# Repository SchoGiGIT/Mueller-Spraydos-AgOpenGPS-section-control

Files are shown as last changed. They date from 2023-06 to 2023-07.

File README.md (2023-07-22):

# Mueler Spraydos AgOpenGPS section control
An electromechanical approach to open source section control of Mueler/Müller Spraydos spraying computers through software as AgOpenGPS. 
This project provides the mechanical design for a non-intrusive addon mod to automatically control the sections on a spraydos computer through a gps system. All needed parts and other information are discribed bellow.

The system consists out of a bracket, that clamps around the spraying computer and doubles as electronics box, and a servo box on a hinge. The main section switch and all other buttons remain freely accessible.

<p float="left">
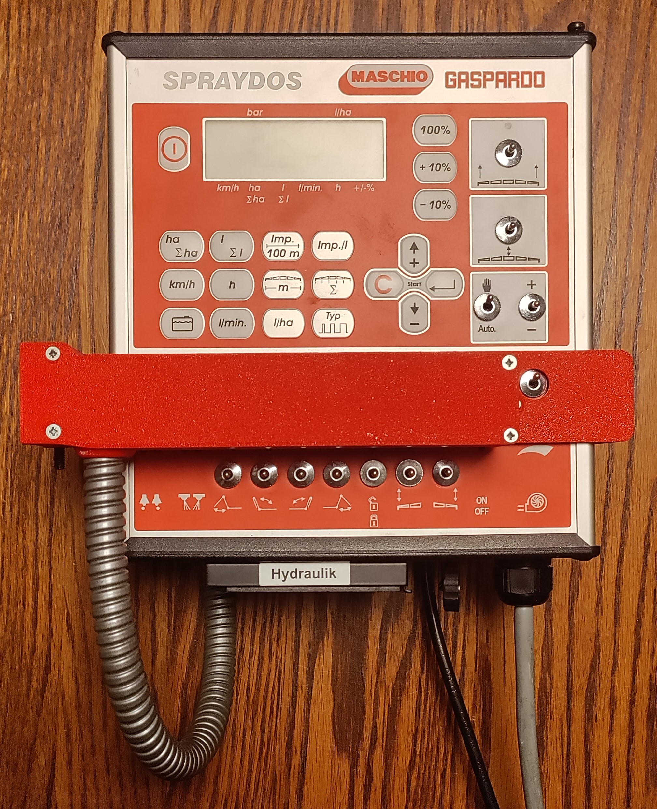
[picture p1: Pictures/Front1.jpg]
  
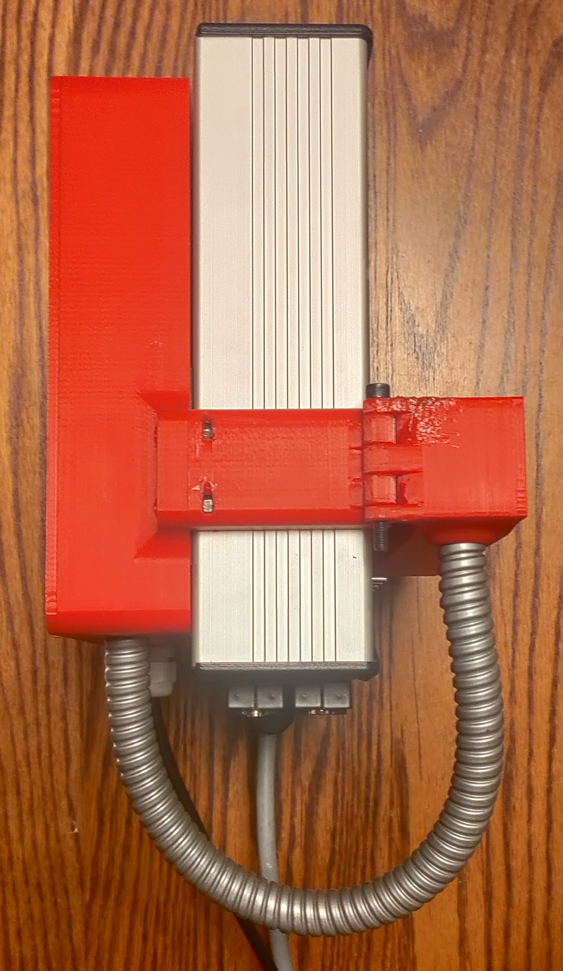
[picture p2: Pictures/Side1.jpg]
  
</p>

The servo box contains servos to control the section switches through specially designed lever arms. The servo box is mounted on a hinge and can be swung away to regain manual control. The servo box can be kept closed through magnets or an M4 bolt
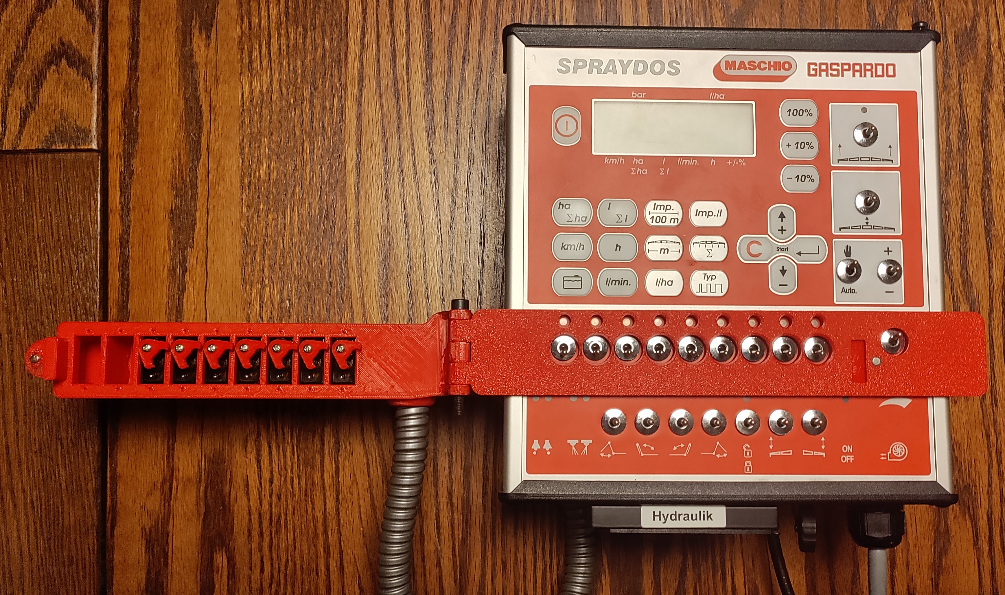
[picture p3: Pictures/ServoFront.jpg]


The electronics box on the back has mounting points to accommodate a 8ch servo controller, A DC buck converter and a 8 channel relay card (optional). The optional relay card can be replaced with a second servo controller when you need 9 sections (mounting holes are there in the new models). Two 16mm holes for input power and section signals and a threaded hole for a sleeve to the Servo box are foreseen.
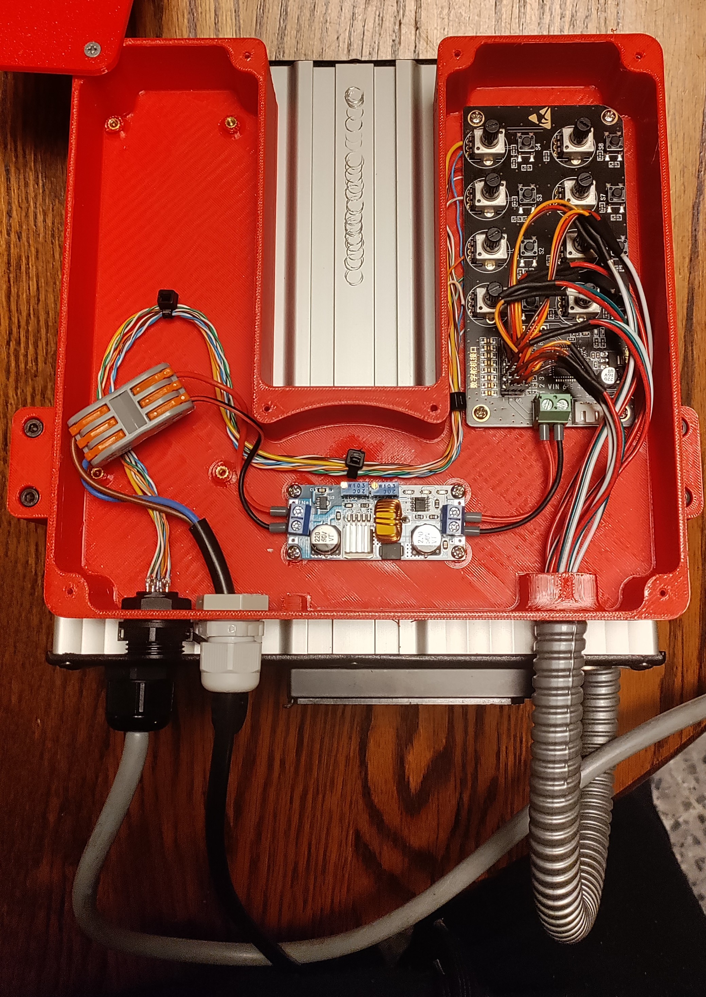
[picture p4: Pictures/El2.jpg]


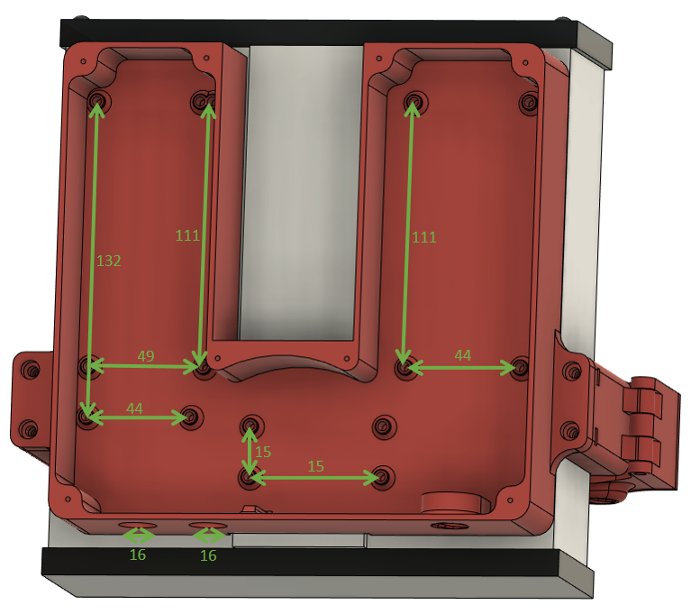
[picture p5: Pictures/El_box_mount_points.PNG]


**_Why control the buttons mechanically and not switch section through relays?_**
* Motorised valves need 2 relays per section (18 in total...).
* You cannot put relays in parallel to the buttons, you will create a short.
* To keep the switches as manual backup they cannot be replaced by relays.
* Breaking the lines going to the the valves and changing the state there with relays could work. But the rate controller will not work anymore since it does not know the real state of the sections. (You could compensate this by changeing the speed signal however)
* To keep the mod as a bolt-on add on to keep the controller original for resale when the time comes.

## Needed hardware
### Printed parts
I provide some limited print service for Western europe. Contact me through github or on [this thread](https://discourse.agopengps.com/t/printing-service-for-aog-community-western-europe/12823)

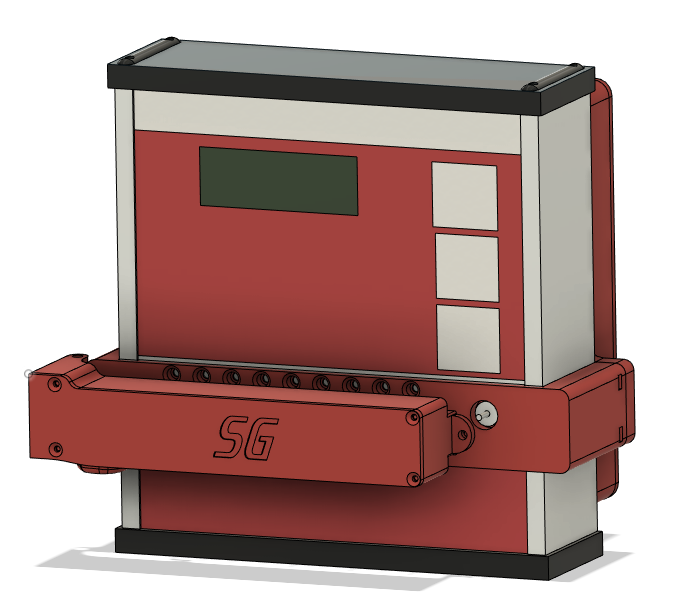
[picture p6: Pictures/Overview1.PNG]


* [Servo box](/Printed_parts/ServoBox.step)
* [Servo box lid](/Printed_parts/ServoBoxLid.step)
* Front bracket
  * [Normal nut](/Printed_parts/FrontBracket.step)
  * [Hotmelt nut](/Printed_parts/FrontBracketHot.step)
* [Electronics box](/Printed_parts/ElBox.step)
* [Electronics box lid](/Printed_parts/ElBoxLid.step)
* [Servo arm](/Printed_parts/ServoArm.step)

### Montage parts
* Wood screw D3 l15 X14 (for al the lids)
* Bolt M4 l15 X4 (for mounting the bracket to the electronics box)
* For mounting the bracket to the electronics box (one of the two)
  * Nut M4 X4
  * Hotmelt nut M4 X4
* Bolt M5 l45 X1 (Serves as hinge bolt)
* Nut M5 X1 (Serves as hinge bolt)
* Hot melt nut M3 X12
* Closing latch (one of the two)
  * Magnet D5 L5 X2 (push in with solder iron)
  * Bolt M4 l8 + Nut M4
* EPDM roofing sheet (+-1mm thick)
  * Glue a big patch or multiple smaller ones on the back of the electronics box. This will provide extra mounting friction and adapt better to the uneven surface of the spraydos controller  

### Electronics
For more than 8 sections you will need two servo controllers or a different type that can accommodate 9 servos.
* Servo motor MG90S (as many as needed for your sprayer) (other models might fit, did not try)
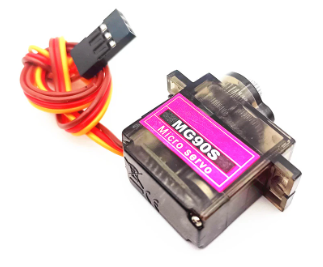
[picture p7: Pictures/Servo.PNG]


* Servo controller, i used [this one](https://nl.aliexpress.com/item/1005002120074314.html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) :
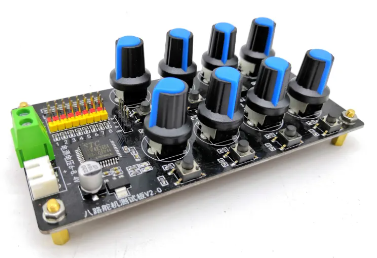
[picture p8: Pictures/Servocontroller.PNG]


* DC buck converter XL4015 5A, mounting holes are compatible with [CC/CV models like this one](https://nl.aliexpress.com/item/1005002554895443.html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) :
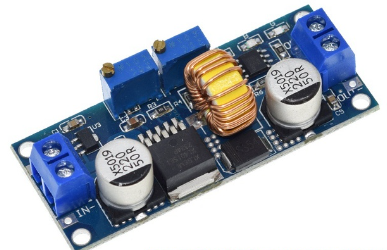
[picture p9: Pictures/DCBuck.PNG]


* Optional 8 way relay module, mounting holes are compatible with [this one](https://nl.aliexpress.com/item/1005002867727977.html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) :
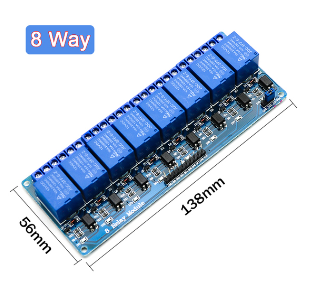
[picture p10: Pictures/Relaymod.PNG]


* Wire nuts, connectors and cable protection
  * Two 16mm holes in electronics box for connections and supply powe
  * Threaded holes in electronics and servo box for flexible armoured cable sleeves (Will probably cahnge this in the future)

## Wiring and control
The servo control needs to be "dumbed down" to a bi-stable state that can be commanded by a section relay card. 
These connections can be switched around based on what kind of section reaction you want to different steering and logic conditions.

### Simple and works but you can create a short circuit!
Use the potentiometer from the servo controller to set one position of the servo arm and bridge the position signal pad (central pin of the potentiometer) to VCC or GND of the servo card with a relay to send it to the second position. Connect these wires to the mount points of the potentiometers on the back of the servo controller card. You only need number of sections+1 cables to control this board.

_Make sure NOT to turn the potentiometers to their full left or right position when relay bridge is closed._

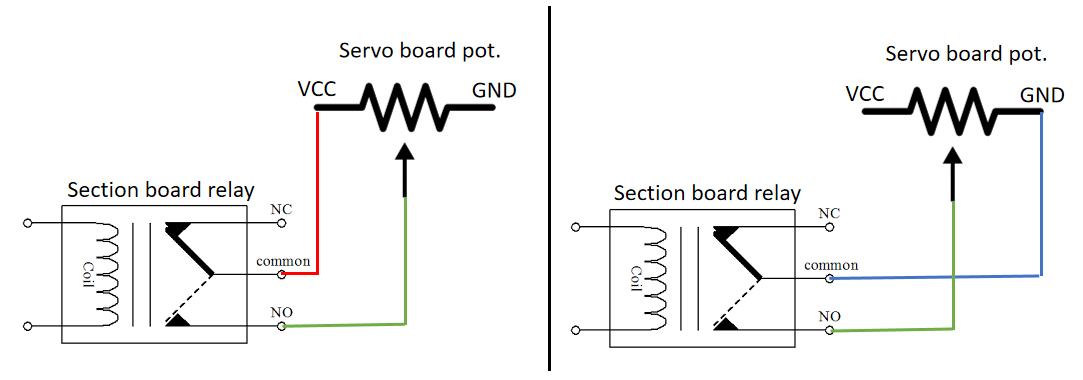
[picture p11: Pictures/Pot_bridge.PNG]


### Safer way but more work
Desolder all the potentiometers from the servo controller board. Connect the common ports of your section relay board to the position signal pads (central pin) of the servo controller board. Connect the VCC and GND of the servo board to a separate pot (reuse on you just took of). Connect the GND and signal of the seperate pot to the NC/NO ports of your section relay board. You only need number of sections+2 cables to control this board. You now use the separate potentiometers to controll one position of all servos and the relay contact for the second position.

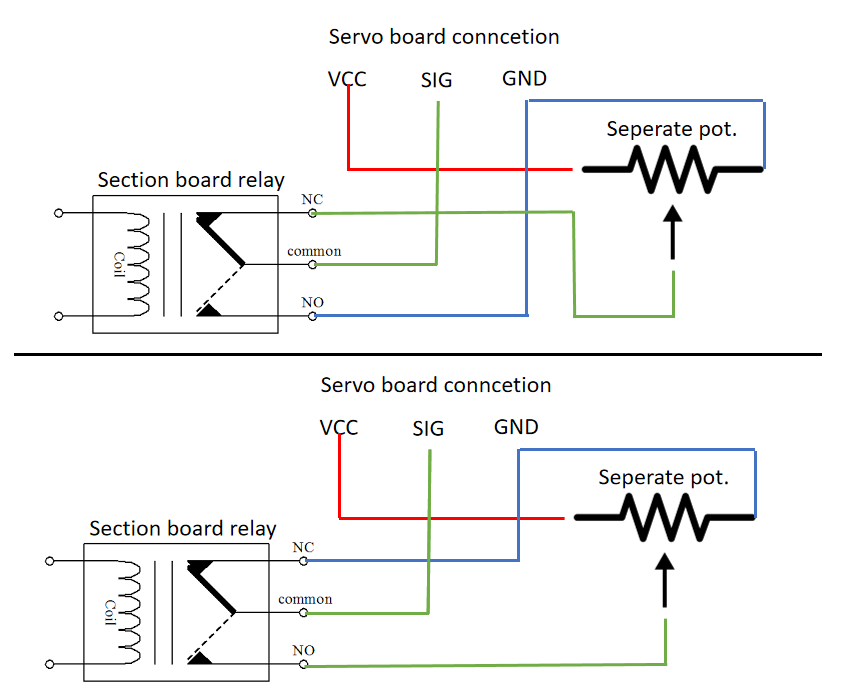
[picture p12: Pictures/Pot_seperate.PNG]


### Better way? use RS485 based servo controller?
TODO

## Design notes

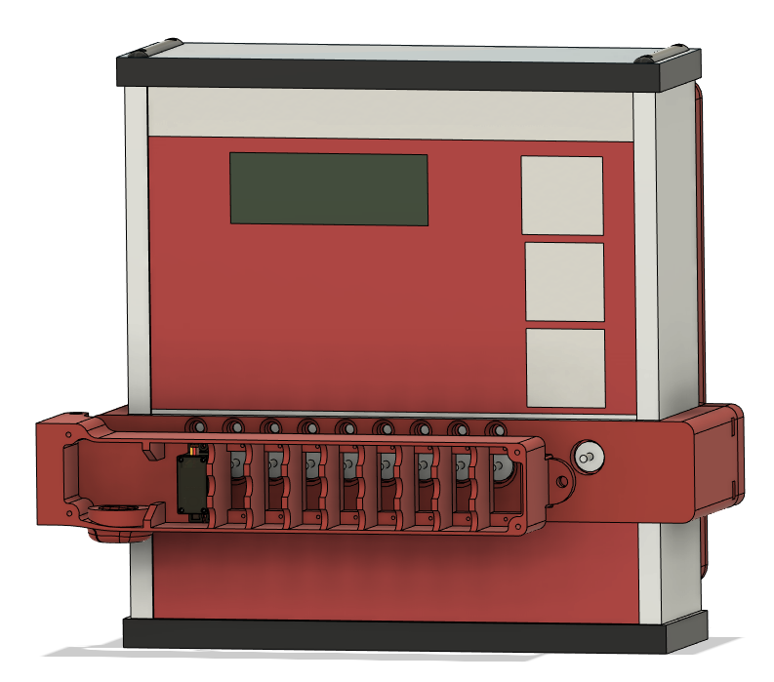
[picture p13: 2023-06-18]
Pictures/Overview2.PNG

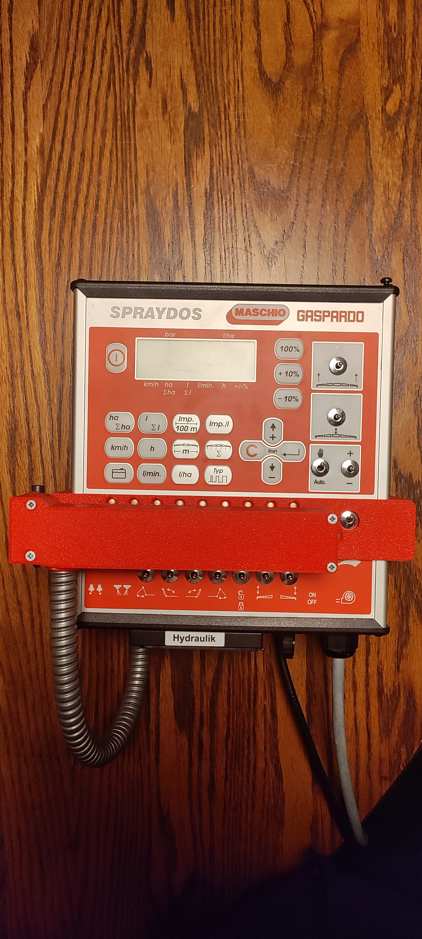
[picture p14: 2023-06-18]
Pictures/Real1.jpg

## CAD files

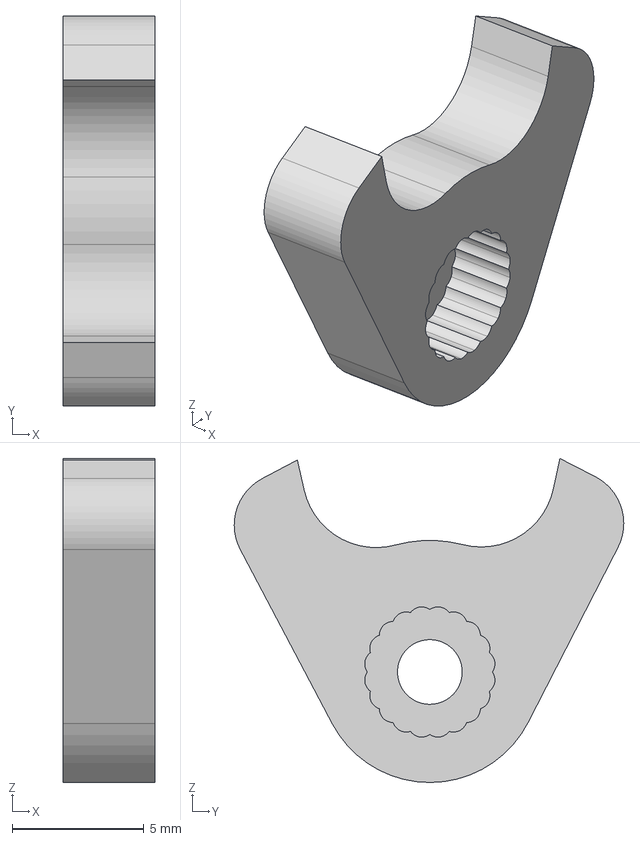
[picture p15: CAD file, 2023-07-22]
Printed_parts/ServoArm.step
3.50 x 14.8 x 12.3 mm

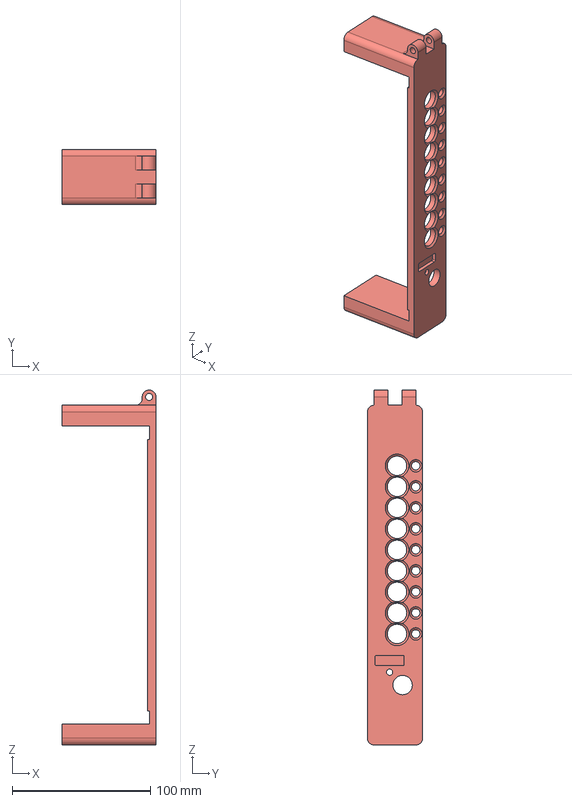
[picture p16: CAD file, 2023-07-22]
Printed_parts/FrontBracketHot.step
68.0 x 40.0 x 256.6 mm

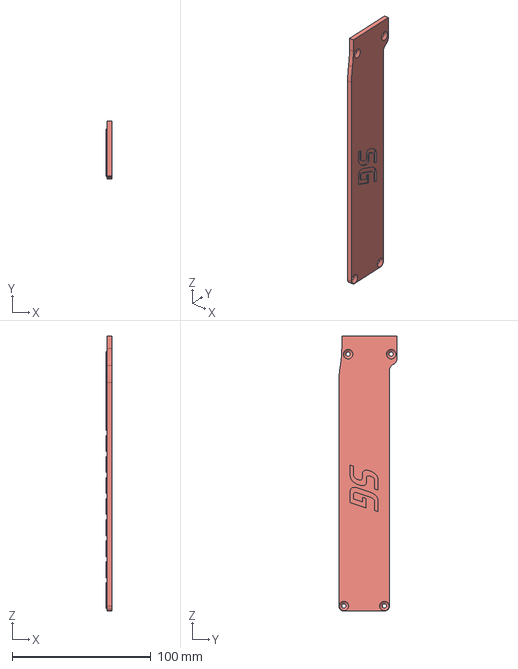
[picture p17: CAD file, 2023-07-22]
Printed_parts/ServoBoxLid.step
4.00 x 42.1 x 198.5 mm

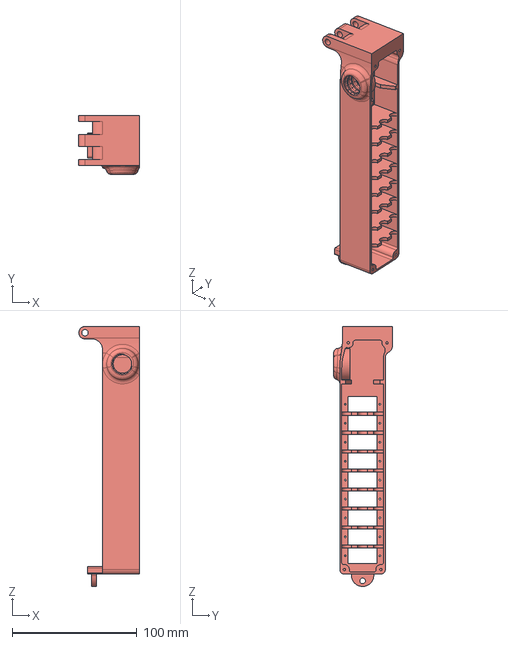
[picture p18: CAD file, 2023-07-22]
Printed_parts/ServoBox.step
48.6 x 47.1 x 208.5 mm

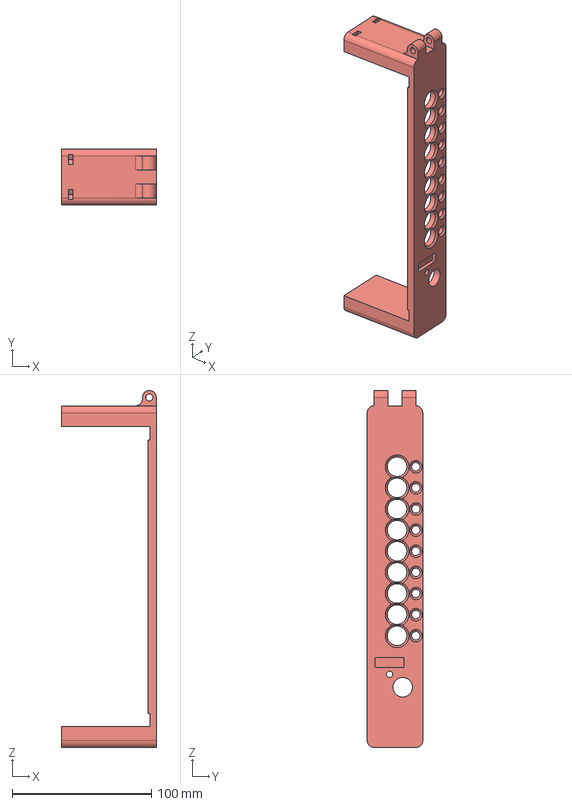
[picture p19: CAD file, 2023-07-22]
Printed_parts/FrontBracket.step
68.0 x 40.0 x 256.6 mm

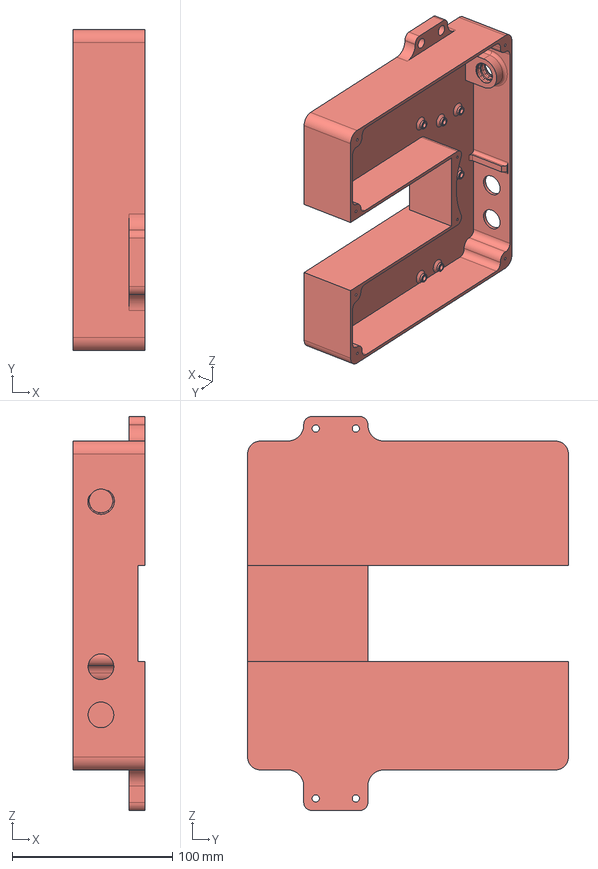
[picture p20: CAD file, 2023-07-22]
Printed_parts/ElBox.step
45.0 x 200.0 x 245.6 mm

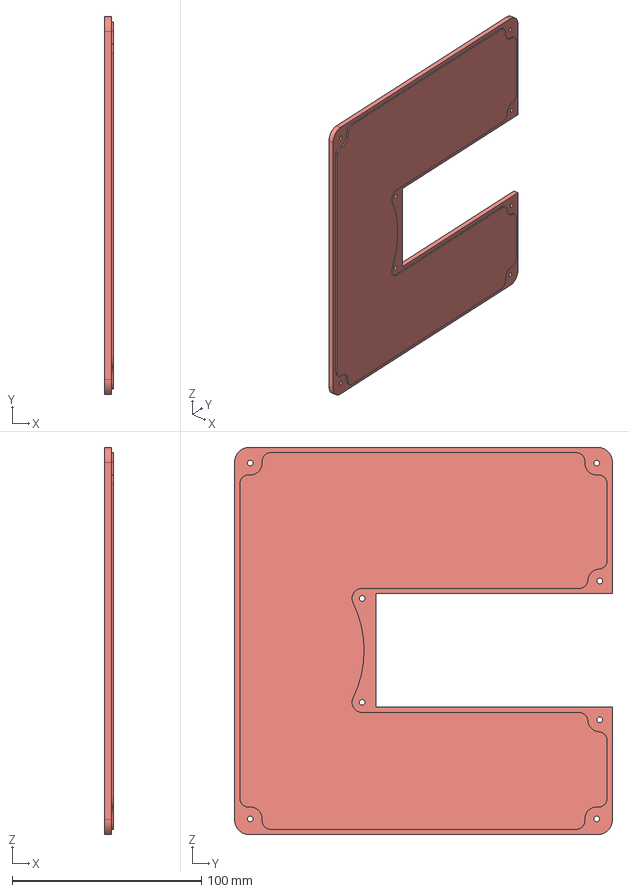
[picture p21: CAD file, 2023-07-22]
Printed_parts/ElBoxLid.step
4.50 x 200.0 x 205.0 mm
